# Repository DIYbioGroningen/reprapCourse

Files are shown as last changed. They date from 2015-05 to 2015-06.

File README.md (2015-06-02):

# reprapCourse
Documentation of the Reprap - 3D printer course

We found latest Prusa i3 printer design, the one Josef Prusa showed at Makerfaire this year in New York, for its elegant simplicity, but hinge like connection between Y axis assembly and frame needed improvement, in our opinion.
Using CAD software we reworked Prusa i3 design:

Laser cut frame was stiffen by adding two angle members connected to the rear side of Y axis assembly.
Original, printed Z Axis mounting parts proven to be easy to break, which is why we replaced them with stronger laser cut parts.
We did not like loose ends on Z Axis lead screw (similar to Printrbot design), therefore we added miniature flanged ball bearing on each side, to support lead screws on the top.
All printed plastic parts were slightly changed, we felt that we should give them additional strength and better cosmetic appearance.
Y axis assembly can be removed and installed back in a minute. Convenient for transportation or shipment.
Dimensions and axis travels of original Prusa i3 preserved.
Test print here:
http://www.youtube.com/watch?v=dZhU4h7qCJY
More Pictures here:
http://www.flickr.com/photos/37863465@N03/8334662257/in/photostream/

Based on: http://www.thingiverse.com/thing:39889

Consider: http://www.thingiverse.com/thing:40064/#files

Consider: http://www.thingiverse.com/thing:182675/#files

Consider: http://www.thingiverse.com/thing:119616/#files

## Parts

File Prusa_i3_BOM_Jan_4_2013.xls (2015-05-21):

ITEM NO. | PART NUMBER | QTY.
1 | Frame, Laser Cut Plywood or MDF, Ver 2 | 1
2 | Stepper Motor, NEMA 17 | 4
3 | Z Shaft 8mm Dia, 320mm, McMaster, 88625K67 | 2
4 | M5 Threaded Rod, 305mm, McMaster, 98861A060 | 2
5 | Phillips Head Screw, M3 x 10, McMaster, 92005A120 | 10
6 | Z Coupler, PVC Tubing 4 ID x 40mm, McMaster, 5006K65 | 2
7 | X Shaft 8mm Dia, 384mm, McMaster, 88625K67 | 2
8 | X End Motor, Printed | 1
9 | Phillips Head Screw, M3 x 20, McMaster, 92005A128 | 4
10 | LM8UU Linear Ball Bearing | 10
11 | Nut, M5, McMaster, 90591A146 | 8
12 | 2GT 24T Pulley, Misumi, GPA24GT2060-B-H5 | 2
13 | Nut, M3, McMaster, 90591A121 | 22
14 | Phillips Head Screw, M3 x 16, McMaster, 92005A126 | 29
15 | X End Idler, Printed | 1
16 | Ball Bearing, 5x16x5 mm, 625ZZ | 4
17 | Phillips Head Screw, M5 x 20, McMaster, 92005A328 | 2
18 | X Carriage for GT2 2mm Belt, Printed | 1
19 | X Belt Clamp, Printed | 1
20 | Phillips Head Screw, M3 x 14, McMaster, 92005A124 | 1
21 | Ball Bearing with Flange, 5x10x4mm, MF105ZZ | 2
22 | Square Nut, M3, Fastenal, 11510909 | 19
23 | Endstop, Printed | 3
24 | Micro Switch | 3
25 | Phillips Head Screw, M2 x16. McMaster, 92005A037 | 6
26 | Nut, M2, McMaster, 90592A004 | 6
27 | Prusa i3, Z Shaft Cup, Prined | 2
28 | Phillips Head Screw, M3 x 12, McMaster, 92005A122 | 12
29 | Y Axis Threaded Rod, 0.325inch x 430mm, McMaster 98914A030 | 2
30 | Y Corner, Printed | 4
31 | Y Shaft 8mm Dia, 405mm, McMaster, 88625K67 | 2
32 | Y Axis Threaded Rod, 0.325inch x 209mm, McMaster 98914A030 | 3
33 | Y Axis Threaded Rod, 0.325inch x 275mm, McMaster 98914A030 | 1
34 | Y Idler for 625ZZ, Printed | 1
35 | Y Motor Mount, Printed | 1
36 | Table , Laser Cut | 1
37 | Y Bearing Holder, Printed | 3
38 | Y Belt Clamp, 2GT 2mm Belt, Printed | 1
39 | Compression Spring, 0.18 x 0.25 Inch, McMaster, 9657K258 | 4
40 | Heat Bed, PCB | 1
41 | Washer, 0.325inch ID, McMaster, 91083A030 | 38
42 | Hex Nut, 0.325-18, McMaster, 95462A030 | 38
43 | 3D Printer Controller Board, Sanguino | 1
44 | Unthreaded Spacer, Nylon, McMaster, 94639A200 | 4

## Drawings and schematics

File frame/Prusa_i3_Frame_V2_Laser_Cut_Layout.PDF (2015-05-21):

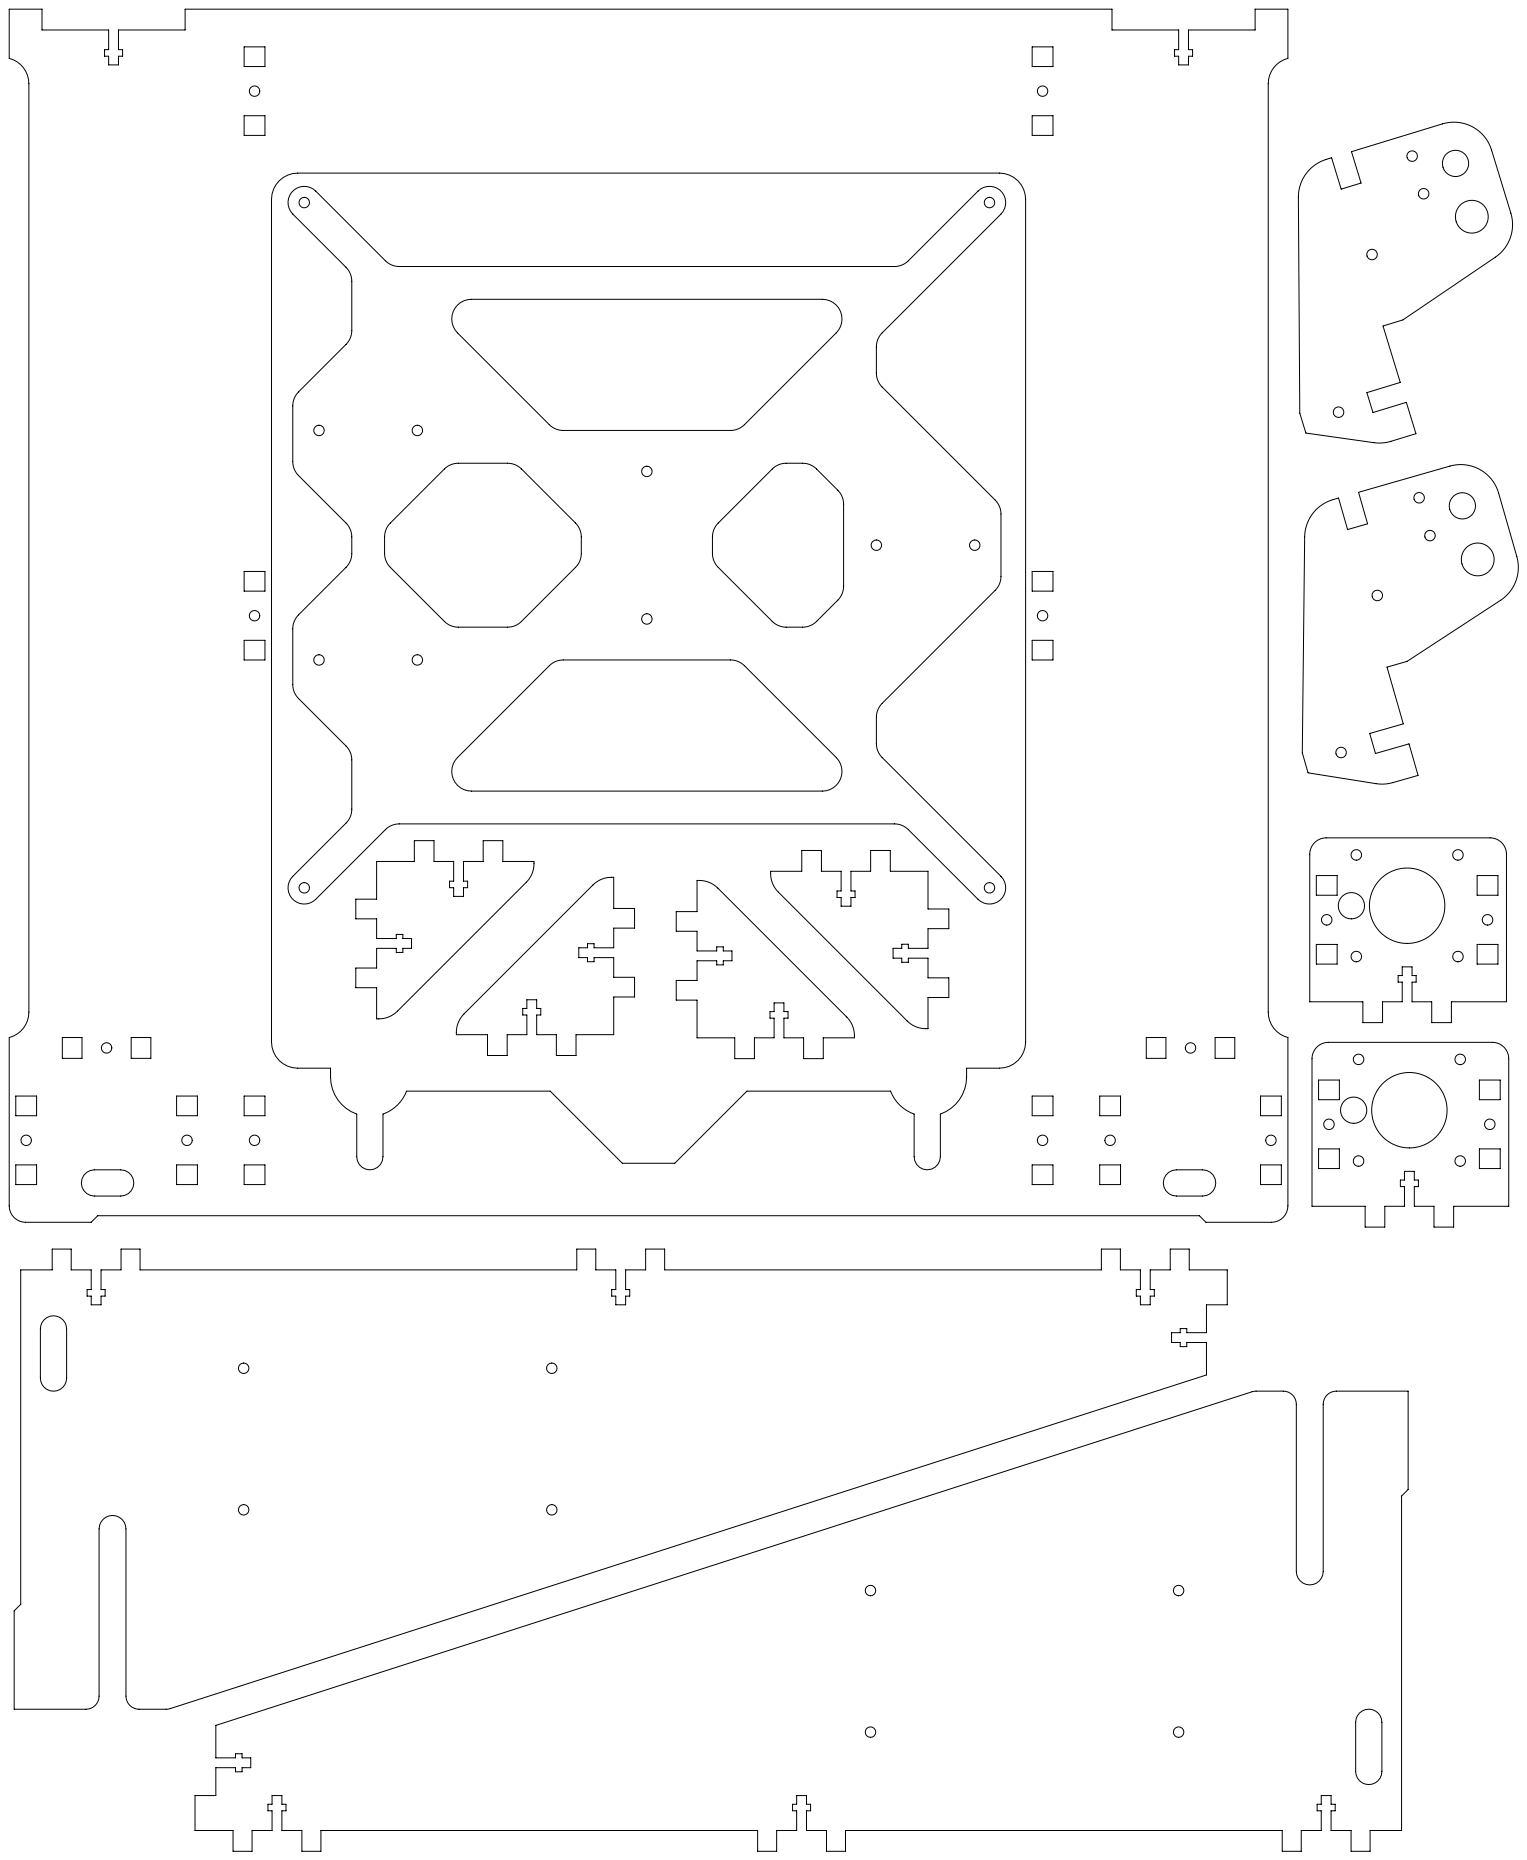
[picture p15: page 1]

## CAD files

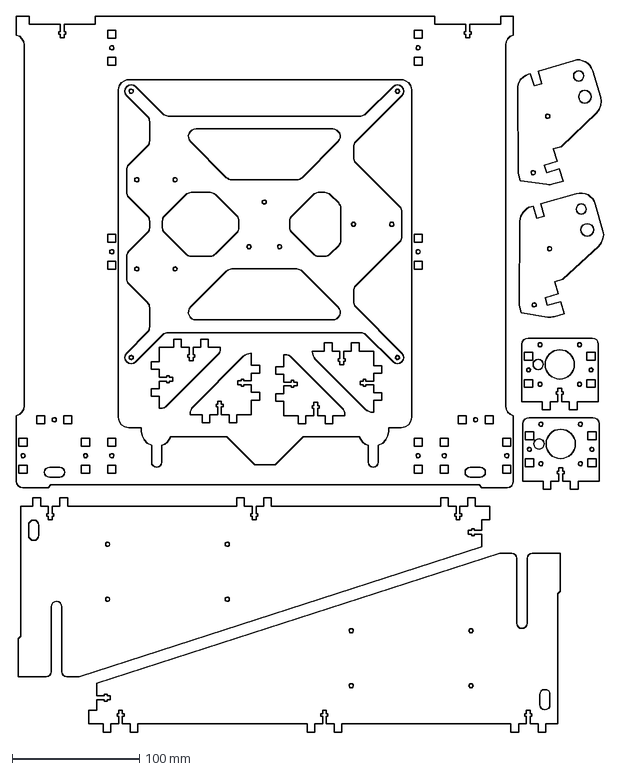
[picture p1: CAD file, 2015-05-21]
frame/Prusa_i3_Frame_V2_Laser_Cut_Layout.DXF
461.5 x 561.8 mm

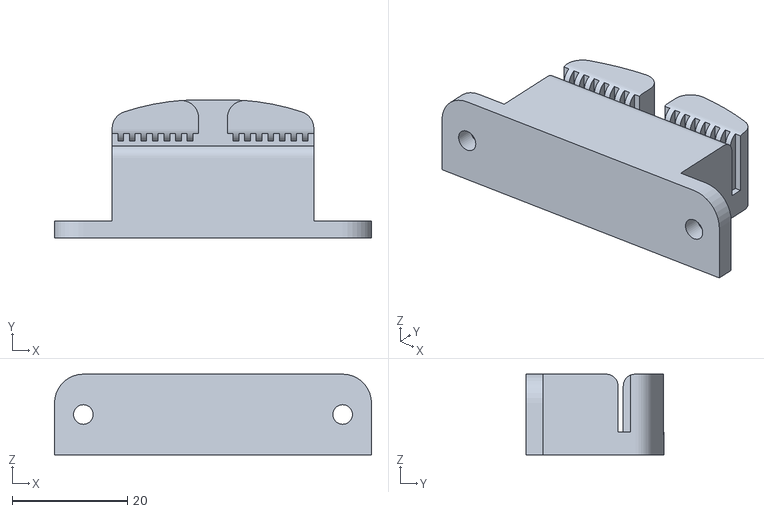
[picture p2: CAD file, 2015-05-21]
printedParts/Prusa_i3_Y_Belt_Clamp_-_0.9mm.stl
55.0 x 24.0 x 14.0

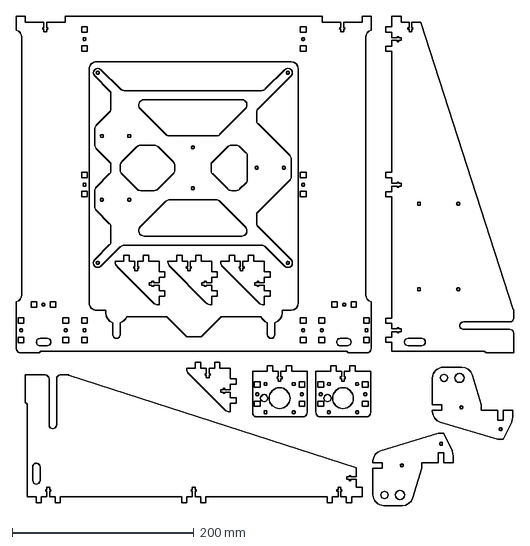
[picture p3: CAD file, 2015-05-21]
frame/Prusa_i3_Frame_V2_Laser_Cut_Parts.dxf
546.5 x 537.8 mm

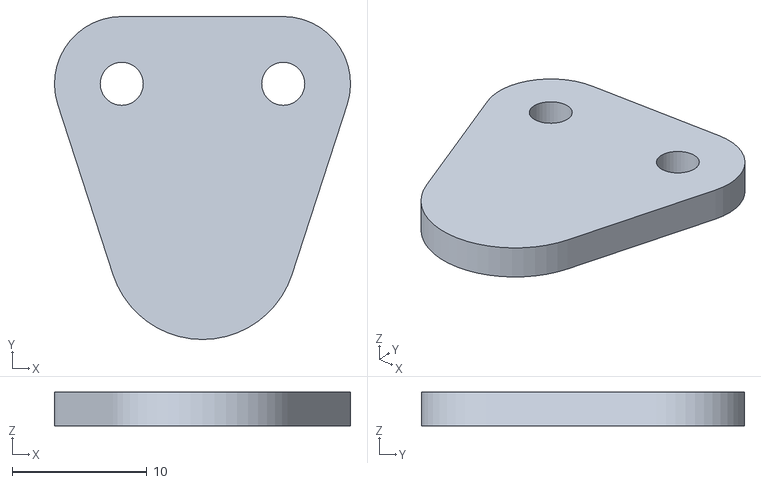
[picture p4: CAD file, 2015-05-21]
printedParts/Prusa_i3_Z_Shaft_Cup.STL
22.0 x 24.0 x 2.50

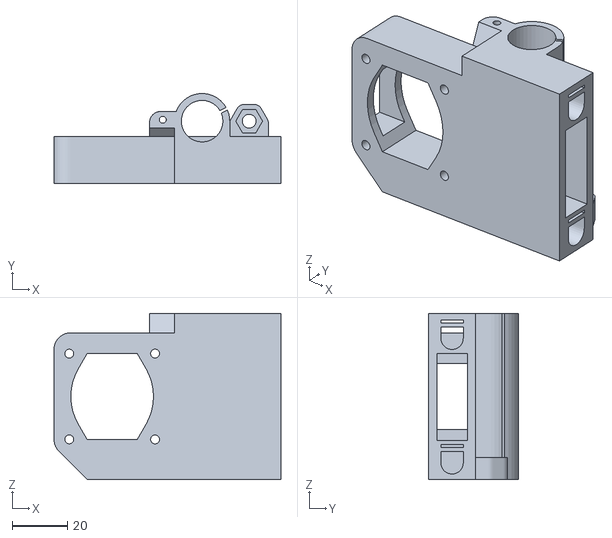
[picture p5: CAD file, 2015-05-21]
printedParts/Prusa_i3_X_End_Motor.stl
82.0 x 32.5 x 60.0

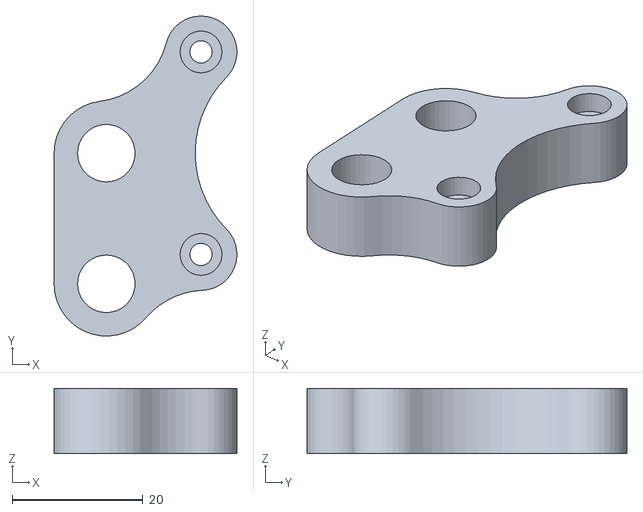
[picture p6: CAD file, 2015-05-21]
printedParts/Prusa_i3_Y_Motor_Mount.stl
28.0 x 49.0 x 10.0

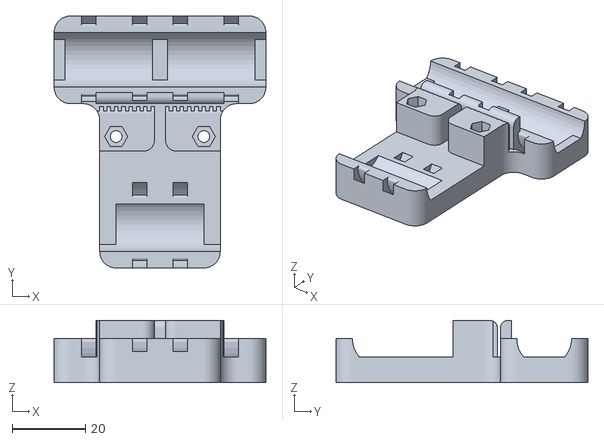
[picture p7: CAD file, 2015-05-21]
printedParts/Prusa_i3_X_Carriage.stl
58.0 x 69.0 x 17.0

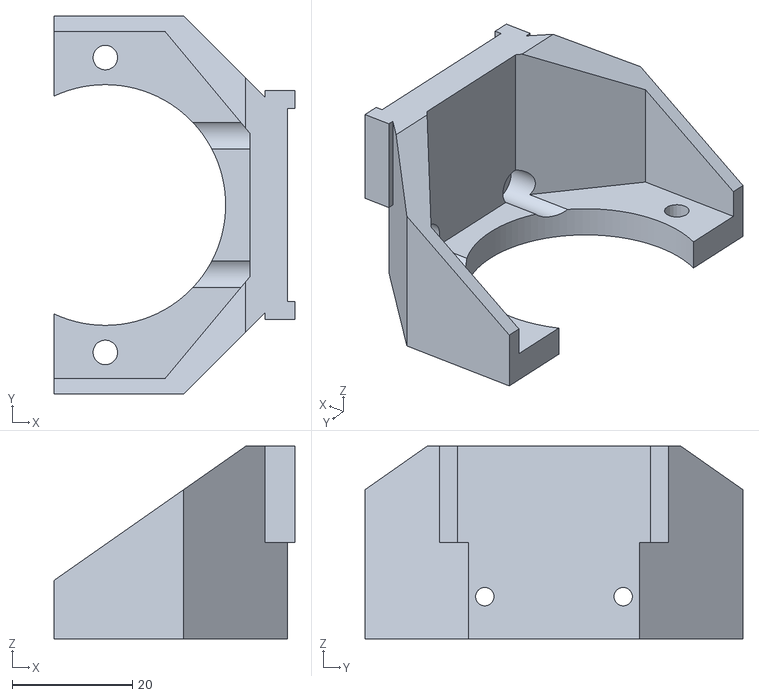
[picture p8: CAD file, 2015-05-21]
printedParts/buddasch_i3.stl
40.0 x 62.8 x 32.0

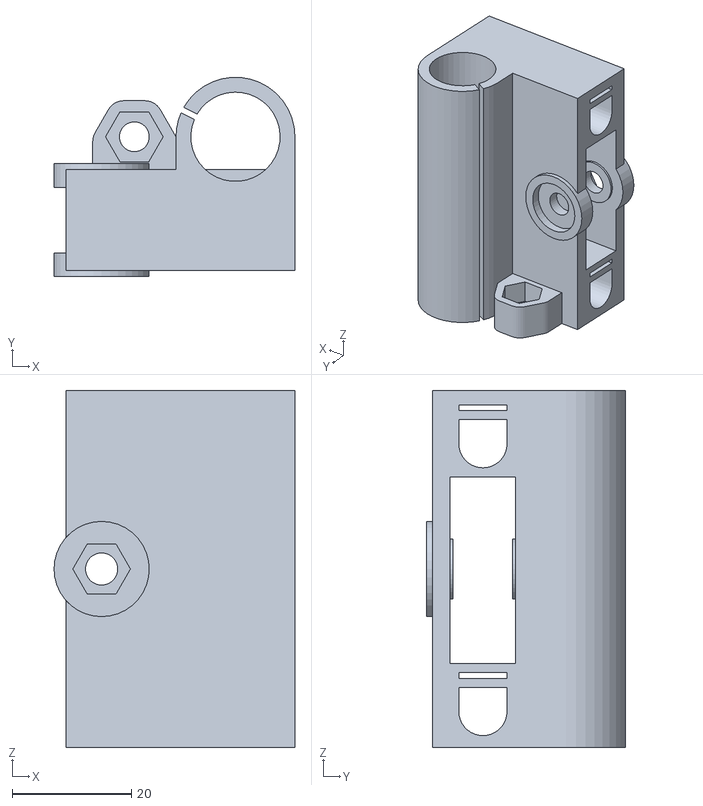
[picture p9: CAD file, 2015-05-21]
printedParts/Prusa_i3_X_End_Idler.stl
40.5 x 33.5 x 60.0

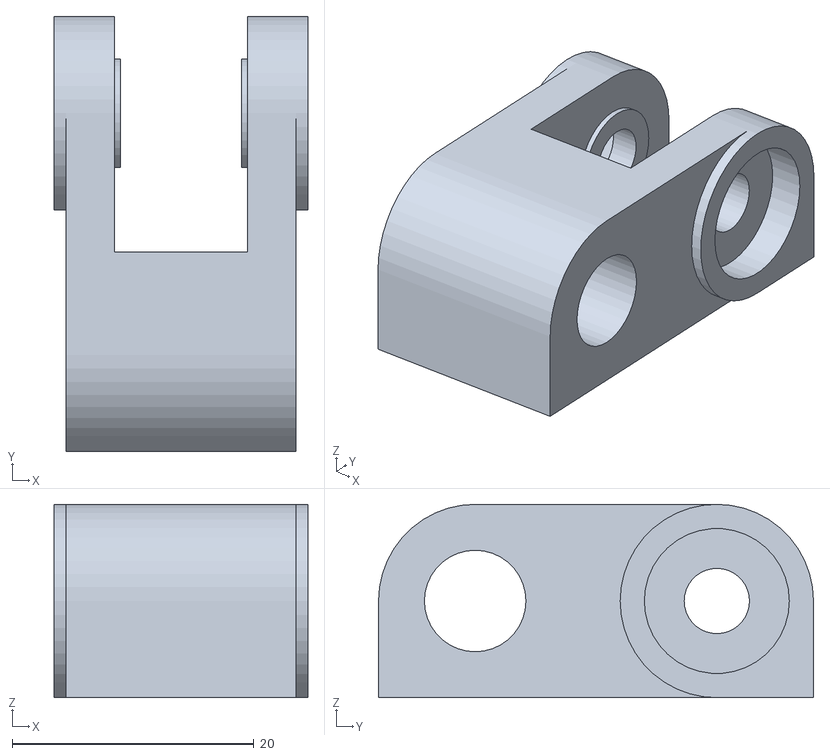
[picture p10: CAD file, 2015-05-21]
printedParts/Prusa_i3_Y_Idler.stl
21.0 x 36.0 x 16.0

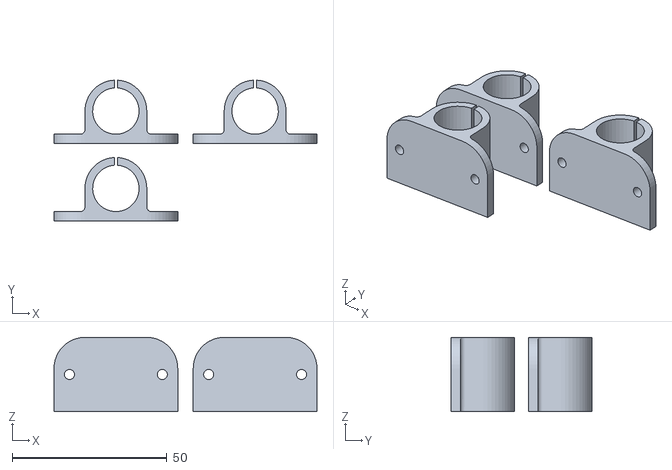
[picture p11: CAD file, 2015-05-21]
printedParts/Prusa_i3_3_x_Y_Busing.stl
85.0 x 45.5 x 24.0

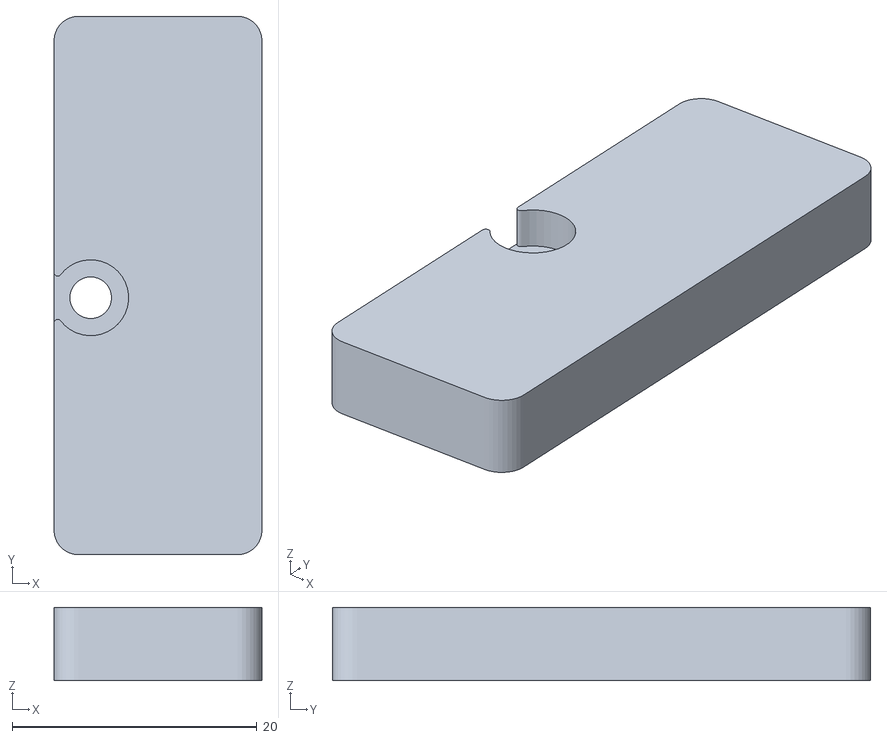
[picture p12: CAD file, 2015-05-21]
printedParts/Prusa_i3_X_Carriage_Belt_Clamp.stl
17.0 x 44.0 x 6.00

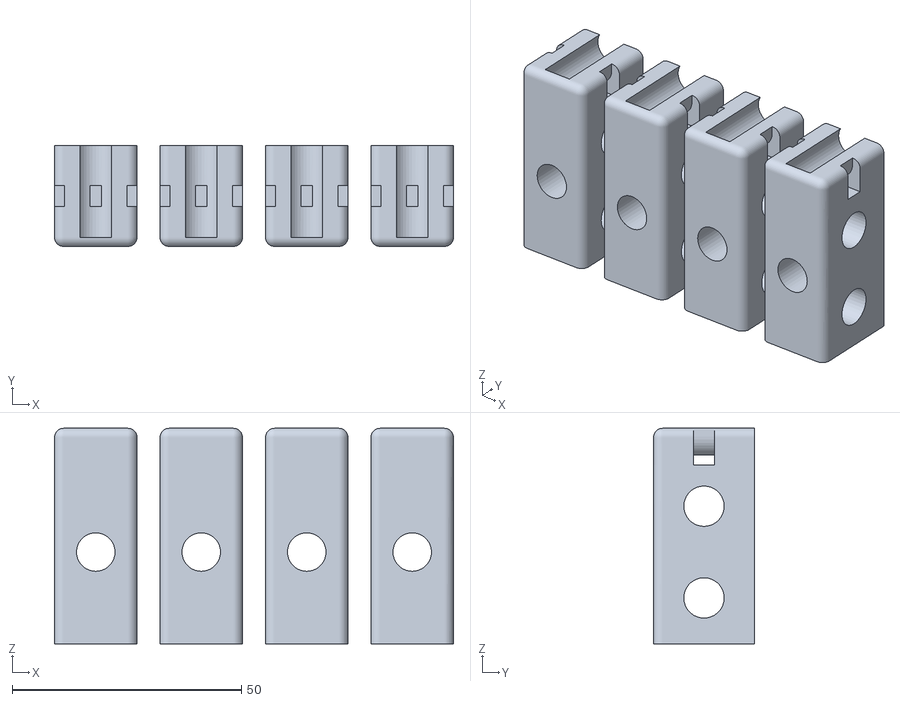
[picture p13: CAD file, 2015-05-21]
printedParts/Prusa_i3_4_x_Y_Corners.stl
87.0 x 22.0 x 47.0

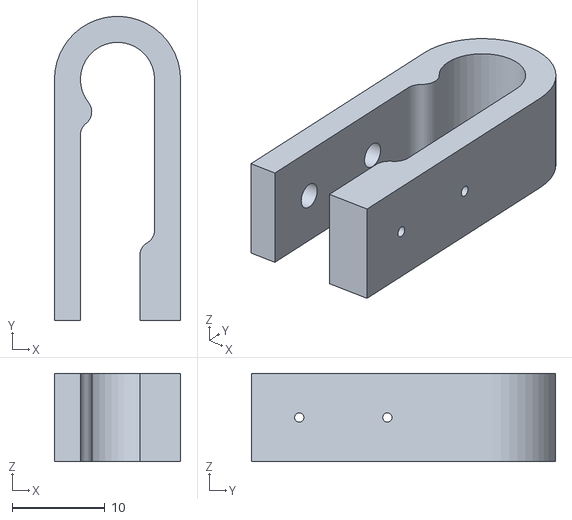
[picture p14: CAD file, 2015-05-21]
printedParts/Prusa_i3_Endstop.stl
13.6 x 32.8 x 9.53
